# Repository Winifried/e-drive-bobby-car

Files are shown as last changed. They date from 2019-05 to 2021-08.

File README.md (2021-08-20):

# e-drive-bobby-car
Bobby car with electric motor - hardware, sofware and how it was put together. 

I always wanted to refurbish a car, now I refurbished my old bobby-car adding an electric motor and some additional lights. I had a hard time finding the parts that fit together well, so over time I created different bobby-car versions. Here's a short overview:

## Version 1: Forward, Backward, Motor Control
This was my first attempt. The car essentially has, next to the stearing wheel, one major power switch for safety, an "ignition key" which turns on the front and rear lights and a trottle control. Depending on the position of the trottle the car is in "neutral" (middle), "reverse" (below neutral) or "drive" (above neutral). The distance from the middle position determines the motor speed. 

Heres the setup:
  
BobbyCar_V1

Forward (left) and (possibly the only true reason requiring) reverse (right): </br>




However, somehow the motor control did not work out very well and got super hot (which is bad as it was attached to plastic). So I created Version 2. 

## Version 2: Forward, Backward, full speed
This is essentially the above described version without motor controller, so it will only go full speed - forward and backwards. 


## Version 3: Forward, Motor Control
The battery turned dead, the acceleration potentiometer broke and essentially there is not much need for a backward gear and I still had a motor controller available. This is why version 3 thus lost its ability to go backwards but when going forwards you can at least control your speed.

BobbyV3_final



## Hardware parts list 
Check the subfolder 'parts' for the 3D printed additions and more details. 

|  component 	| included in all versions |  Version 1  	| Version 2 	| Version 3 	|
|:-:	|:-:	|:-:	|:-:	|---	|
| board  	| arduino uno 	| 	| 	| 	|
| lights  	|  4 LED (front: 2 white, rear: 2 red) 	| 	| 	| 	|
| battery  	|  - 	|  12V 5Ah [Maxtuned SLA4L-BS Lead Acid] 	| 12V 5Ah [Maxtuned SLA4L-BS Lead Acid]  	| 12 V 9.8Ah [VariCore  Li-Ion] 	|
| speed control  	|  - 	| Foxnovo 6V-90V 15A DC Motor Speed Controller Switch  	|  none 	| DC Brush Motor Speed Control PWM XY-L-1240 12 V 	|
| engine 	|  12V 100 Watt 2700 RPM (7 tooth sprocket wheel) [option: 12v/24V] 	| 	| 	| 	|

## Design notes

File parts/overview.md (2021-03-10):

**parts**

*hardware*
* bobby car (this one is the classic version) 
* wheels: Big whisper wheels [the old wheels needed replacement]
* engine: 12V 100 Watt 2700 RPM (7 tooth sprocket wheel) [option: 12v/24V]
* battery: 12V 5Ah [Maxtuned SLA4L-BS]
* lights: 4 LED (2 white, 2 red)
* board: Arduino Uno
* 3 relays 
* on/off: rocker switch
* Speed control: Foxnovo 6V-90V 15A DC Motor Speed Controller Switch [not used in final version]

* chain: 25h (pocket bike chain)
* rear sprocket: 25h, 55 teeth, 54mm 
* adjusting ring: A10 [fixating sprocket to rear achsis]

*individualised 3D printing*
* radiator grill
* ignition switch
* cap of throttle [this is actually the ignition switch, only the 3D printing got interrupted midway]

*wood arrangements*
* throttle
* car key

Of note: I didn't find an appropriate metal for the undercarriage and reused the available plastic (very old bobby-car classic version with thick plastic bottom). But this is not something I can recommend. A solid undercarriage is essential to allow full speed. Otherwise, depending on the drivers weight, there is too much bending force on the back axle, reducing the final speed and potentially creating heat...

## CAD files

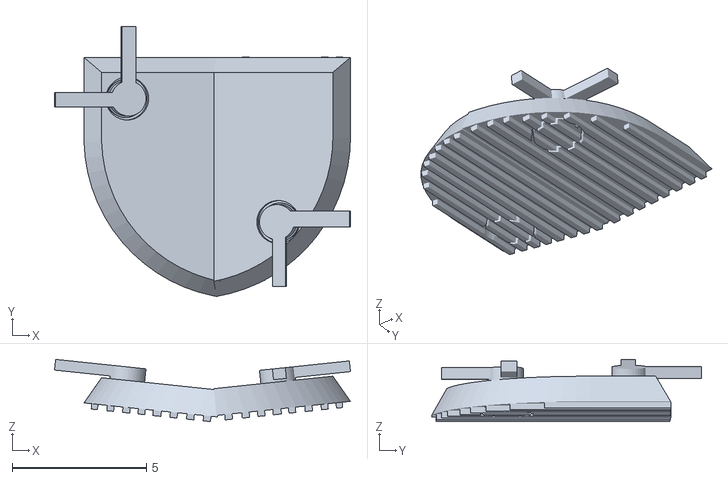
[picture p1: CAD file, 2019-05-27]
parts/radiator_grill.STL
11.0 x 10.0 x 2.31

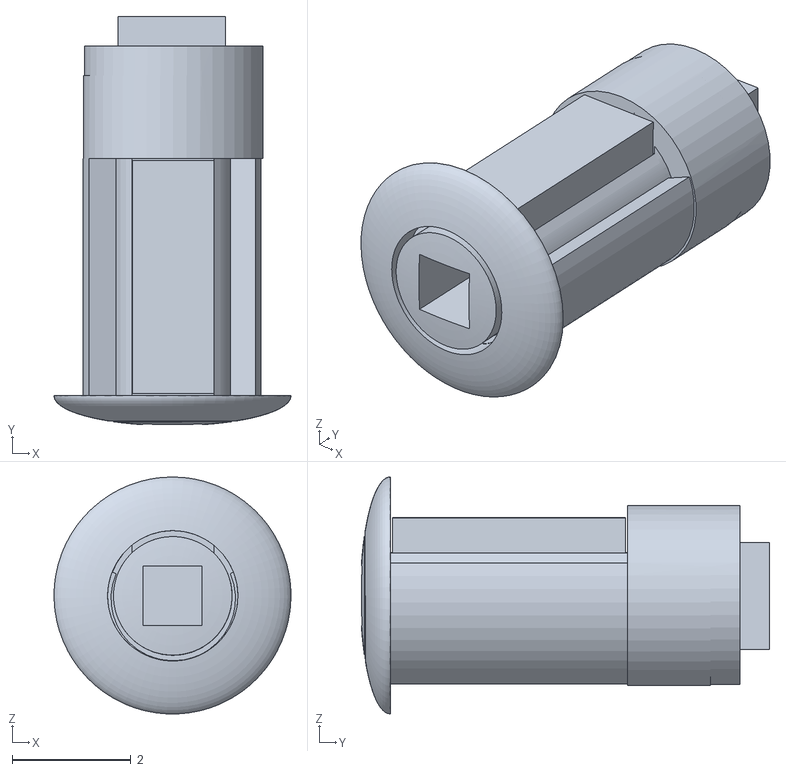
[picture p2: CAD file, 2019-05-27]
parts/ignition_switch.STL
4.00 x 6.89 x 4.00

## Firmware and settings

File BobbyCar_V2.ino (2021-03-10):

/* Arduino Uno
 */

// input pins
int startPin = 2;  // A2: input pin, Potentiometer -> turn car key
int speedPin = 1;  // A3: input pin, Potentiometer -> move gas lever
int lightPin = 12; // D12: output pin, lights (2 LEDS white, paralel)
int backlightPin = 13; // D13: output pin, lights (2 LEDS red, serial)
int motorspeedcontrol = 6; // D6: output pin, give  speed to motor after changing potentiometer value 
                            // has to be a digital pwd pin, even when using analogwrite

int relais_1 = 9 ; // D9: output pin, Relais ground turn 12V off when switching current direction 
int relais_2 = 10; // D10; output pin, Relais switch current 1
int relais_3 = 11; // D11; output pin, Relais switch current 2

int go = 0;        // value car key turn
int vroom = 0;     // value gas lever
int old_vroom = 0; // trying to dejitter
int true_vroom = 0; // value new output to motorspeedcontrol
int dlay = 0; // delay value in while loop

//volatile bool turn_on = false;
volatile bool car_on = false;
volatile bool dir_forward = true ;
volatile bool prev_dir = true;


// output pins 


void setup() {
 Serial.begin(9600);                        // display | debugging 
 Serial.println("starting setup...");
 pinMode(lightPin, OUTPUT);                 // light as output
 pinMode(backlightPin, OUTPUT);             // light as output
 pinMode(motorspeedcontrol, OUTPUT);  
  analogWrite(motorspeedcontrol, true_vroom);
 pinMode(speedPin, INPUT);
 pinMode(startPin, INPUT); 
 pinMode(relais_1, OUTPUT);
  digitalWrite(relais_1, LOW);
 pinMode(relais_2, OUTPUT);
  digitalWrite(relais_2, HIGH);
 pinMode(relais_3, OUTPUT);
  digitalWrite(relais_3, LOW);
 
 Serial.print("Keypoti reads: ");
 Serial.println(go);
 Serial.println("Gaspoti reads: ");
 Serial.println(vroom);
 Serial.println("dir_forward :");
 Serial.println(dir_forward);    
 
}

void direction() {
  if (dir_forward == true) {
      digitalWrite(relais_1, LOW);
      Serial.print("relais_1 LOW - switching circuit start");
      delay(5);
      digitalWrite(relais_2, HIGH);
      digitalWrite(relais_3, LOW);
      Serial.print("relais_2 HIGH, relais_3 LOW - going forwards");
      delay(5);
      digitalWrite(relais_1, HIGH);
      Serial.print("relais_1 HIGH - switching circuit end");
  }
  if (dir_forward == false) {
      digitalWrite(relais_1, LOW);
            Serial.print("relais_1 LOW - switching circuit start");
      delay(5);
      digitalWrite(relais_2, LOW);
      digitalWrite(relais_3, HIGH);
            Serial.print("relais_2 LOW, relais_3 HIGH - going backwards");
      delay(5);
      digitalWrite(relais_1, HIGH);
            Serial.print("relais_1 HIGH - switching circuit end");      
  }
}

void loop() {
  go = analogRead(startPin);        // read out car key turn
  vroom = analogRead(speedPin);     // read out gas lever
  vroom = analogRead(speedPin);     // read out gas lever twice to reduce jitter/bounce

  if (vroom < (old_vroom - 2.5) || vroom > (old_vroom + 2.5)) {
    old_vroom = vroom;
  } else {
    vroom = old_vroom;
  }
   
   if (go > 300) {
    digitalWrite(relais_1, HIGH);
    digitalWrite(lightPin, HIGH); // turn front lights on
    digitalWrite(backlightPin, HIGH); // turn back lights on
    
   if (vroom > 450 ){
    dir_forward = false;                         // going backwards

             // Serial.print("dir_forward False ");
             // 550 = 0
             // 780 = 1017
    true_vroom = 1023;
    //true_vroom = map(vroom, 350,500,500, 1023);  // map the range of true_vroom to the readout of vroom
    analogWrite(motorspeedcontrol, true_vroom);  // change the analog out value
    //motorspeed= vroom;
    // (vroom-800);
              Serial.print("vroom value: ");
              Serial.print(vroom);
              Serial.print("\t motorspeed (true_vroom): ");
              Serial.println(true_vroom);
             // Serial.print("motorspeed & direction: ");
             // Serial.println(motorspeed, dir_forward);
              //Serial.println(dir_forward);
              Serial.print("\t going backwards ");

     dlay = 0;
     while (dlay < 50) {
     analogWrite(motorspeedcontrol, true_vroom);
     dlay++;
     }
                                        // delay(50) wait 50 ms before the next loop for the analog-to-digital converter 
                                                  // to settle after the last reading
    
   } else if (vroom >=300 && vroom <=450 ) {
      digitalWrite(relais_1, LOW);
      Serial.print("relais_1 LOW - motor off");
             // Serial.print("dir_forward do nothing ");
             true_vroom=0;
             analogWrite(motorspeedcontrol, true_vroom);
              Serial.print("vroom value: ");
              Serial.println(vroom);
              Serial.print("\t motorspeed (true_vroom): ");
              Serial.println(true_vroom);
              Serial.print("\t not moving - switching gears ");
     dlay = 0;
     while (dlay < 50) {
     analogWrite(motorspeedcontrol, true_vroom);
     dlay++;
     }
     //delay(50);
   } else {
    dir_forward = true;
    true_vroom = map(vroom,  300,0, 500, 1023);  // map the range of true_vroom to the readout of vroom
    //analogWrite(motorspeedcontrol, true_vroom);  // change the analog out value
    true_vroom = 1023;
    //motorspeed=vroom;
    //1024-vroom;
              Serial.print("vroom value: ");
              Serial.println(vroom);
              Serial.print("\t true motorspeed: ");
              Serial.println(true_vroom);
              //Serial.print("motorspeed & direction: ");
              //Serial.println(motorspeed);
              //Serial.println(dir_forward);
              Serial.print("\t going forward ");
     dlay = 0;
     while (dlay < 50) {
     analogWrite(motorspeedcontrol, true_vroom);
     dlay++;
     }
     //delay(50);
   }
    //Serial.print("turning lights on");
  }
  else {
    digitalWrite(lightPin, LOW); // turn lights off
    digitalWrite(backlightPin, LOW); // turn lights off
    true_vroom=0;
    analogWrite(motorspeedcontrol, true_vroom);
    digitalWrite(relais_1, LOW);  
              Serial.print(" lights off, motor off ");
              Serial.print("\t motorspeed value (vroom): ");
              Serial.println(vroom);
              //Serial.println("dir_forward: ");
              //Serial.println(dir_forward);  
    delay(50);
          
  }

 if (dir_forward == true && prev_dir != dir_forward) {
      digitalWrite(relais_1, LOW);
      Serial.print("switching current start: relais_1 :");
      Serial.println(relais_1);
      delay(50);
      digitalWrite(relais_2, HIGH);
      digitalWrite(relais_3, LOW);
      Serial.print("switching current: relais_2 HIGH, relais_3 LOW ");
      delay(50);
      digitalWrite(relais_1, HIGH);
      Serial.print("switching current end: relais_1 HIGH ");
      prev_dir = true;
      delay(20);
  }
   if (dir_forward == false && prev_dir != dir_forward) {
      digitalWrite(relais_1, LOW);
            Serial.print("switching current start: relais_1: ");
      delay(50);
      digitalWrite(relais_2, LOW);
      digitalWrite(relais_3, HIGH);
            Serial.print("switching current : relais_2 LOW, relais_3 HIGH ");
      delay(50);
      digitalWrite(relais_1, HIGH);
            Serial.print("switching current end: relais_1 HIGH "); 
      prev_dir = false;     
      delay(20);
  }
  
}
